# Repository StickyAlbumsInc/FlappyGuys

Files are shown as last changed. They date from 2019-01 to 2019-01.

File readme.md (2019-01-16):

Flappy Guys
==============

This repo contains the source code, materials list, STL files, patterns, and instructions for creating and assembling a group of 5 IR controlled, miniature "flappy guys," more boringly referred to as "air dancers" or "windsock people."

These guys, but small:



The inspiration for this project came about during a team meeting in which we lamented how loud and ineffective (and not remote controlled) current miniature "flappy guys" on the market are. We knew we could do it better! So this became a thing. Here is that thing.

The parts can add up, but many of them are things you'll probably have on hand already, if you work with Arduino. Many of the links on the parts are for bulk buying options, which gives you a little more up-front cost but a much lower cost-per-unit. If you plan to make a hobby out of Arduino, it's worth the investment, as these are common parts you will likely use often (header pins, DC jacks, solderable breadboards, etc.). 

It also helps if you have access to a 3D printer to print a shroud for each fan in your final build. If you can't 3D print one, you will need to fabricate a similar shroud in some fashion. There are a number of ways this could be done and some of those will be discussed in the build guide.

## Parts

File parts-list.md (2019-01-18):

Parts List
====

Essential Parts
----

These are the essential parts necessary for building the Flappy Guys array. 

* Arduino Uno - [link](https://www.amazon.com/Elegoo-EL-CB-001-ATmega328P-ATMEGA16U2-Arduino/dp/B01EWOE0UU)
* 12v DC power supply - [link](https://www.amazon.com/gp/product/B0725QLQH5)
* 5 90mm three-wire PWM PC cooling fans - [link](https://www.ebay.com/itm/90mm-3-pin-sleeve-Bearing-Computer-Case-cooling-Fan-plug-to-the-motherboard/302927138516)
* IR remote control and sensor board - [link](https://www.amazon.com/gp/product/B01EE4VXS0)
* 5 IRF530N MOSFET transisters - [link](https://www.ebay.com/itm/5Pcs-IRF530NPBF-IRF530N-TO-220-Ir-Power-Mosfet-US-Stock-v/132669538850)
* 18GA solid core wire
* 30x60in piece of ripstop nylon in a color of your choice (or multiple colors) - [link](https://www.amazon.com/gp/product/B07688SRPS)
* 24x36in sheet of black foam core - or some other material to construct the base (wood, plastic, metal) - buy this locally
* A few male-female Dupont jumper wires

Optional Parts
----

The parts below are optional, but having them will make your build easier and much cleaner. Without these parts, you could connect all of the pieces above with wire and solder them all together. Using the parts below, you'll be able to construct a board that all of your fans and your Arduino will plug into.

The build guide will assume you have the optional parts. If not, it's pretty easy to figure out how to omit them. 

* 5.5mm DC power jack - [link](https://www.amazon.com/gp/product/B01N5TW8P5/ref=ppx_yo_dt_b_asin_title_o03__o00_s01?ie=UTF8&psc=1)
* Solderable breadboard - [link](https://www.amazon.com/Gikfun-Solder-able-Breadboard-Plated-Arduino/dp/B071R3BFNL)
* Heat shrink tubing - [link](https://www.amazon.com/gp/product/B01M6YB9CB)
* Header pins - [link](https://www.amazon.com/Header-Lystaii-Pin-Connector-Electronic/dp/B06ZZN8L9S)
* 5 3-pin 10in CPU fan extension cables - [link](https://www.ebay.com/itm/10Pcs-12V-3-Pin-Female-to-3Pin-Male-PC-Fan-Power-Splitter-Extension-Cable-Wire/162980280013)

Tools & Misc. Materials
---
* 3D printer - [a great, affordable option](https://www.amazon.com/Anycubic-Upgraded-PRINTER-Heated-Screen/dp/B074NZPHJ5)
* Soldering iron - [my personal favorite](https://www.amazon.com/Bundle-Soldering-Station-CHP170-cutter/dp/B00AWUFVY8)
* Solder - [I use this](https://www.amazon.com/gp/product/B0006O933K)
* Breadboard - If you're confused on the wireing you can test before soldering
* Utility Knife (or Sword of Exact Zero)
* Carpenter's square or T-square (or a ruler and more patience)
* Compass (or 3in round lid, etc. to trace around) 

If your base is made of Foam Core:

* Hot glue gun & glue sticks
* E6000 Epoxy
* Straignt pins
* White glue
* Small paint brush
* Scissors
* Cutting Mat

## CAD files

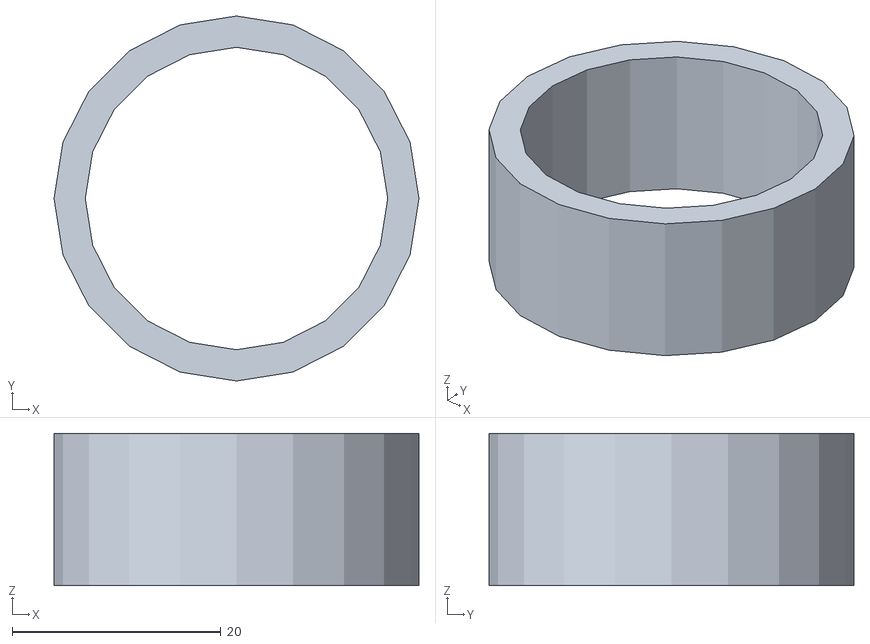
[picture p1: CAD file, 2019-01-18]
tension-ring.stl
35.0 x 35.0 x 14.6

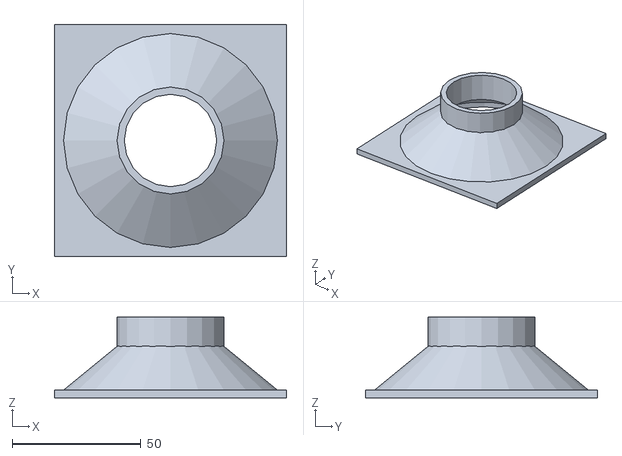
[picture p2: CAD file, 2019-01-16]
fan-shroud.stl
90.0 x 90.0 x 31.3

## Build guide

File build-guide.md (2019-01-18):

Build Guide
=============

1. Setting Up The IR Sensor
2. Updating Up The Control Code
3. Prototyping Single Fan Writing
4. Building The Control Board
5. Connecting & Testing
6. Fabricating The Fan Shrouds
7. Constructing Nylon Flappy Guys
8. Building The Base
9. Putting It All Together

### 1. Setting Up The IR Sensor

Let's go ahead and get the code side of this project out of the way, since it's the easiest. The pvodied `control-code.ino` file contains everything you need to start/stop your five flappy guys, but you'll probably need to change the IR input values, depending on your IR remote. 

So the first step is finding these values.

To do this, first begin by plugging your IR receiver into your Arduino. This shouldn't be a parmanent connection at this point, just temporarily connect the IR receiver with jumper wires as indicated below.

IR Wiring

Next, plug your Arduino into your computer and open `ir-read-utility.ino` in your Arduino IDE. In the tools menu, make sure you have the right COM port selected and flash the read utility code to your Arduino. 

Once you've flashed the board, open the serial monitor (Tools > Serial Monitor). 

Now start pressing buttons on your remote. In my build, I used buttons 1-5 to control each of the 5 fans, and used a big red center button in the middle of the remote to toggle everything off/on. 

It doesn't really matter what order you assign buttons in, so long as it's logical to you. Using numbers 1-5 makes the most sense, though, so I'll assume you're doing that! 

Whenever you press a button on the remote, you should see an integer displayed in the serial monitor. You'll want to make note of which integers belong to which buttons.

Please note, with these inexpensive IR sensors, it's very easy to get interference. As I was working on this, my heartrate sensor from my Fitbit kept interfering with the IR sensor when my wrist was next to it. 

So push buttons a few times and make sure you're getting consistent readings! Recode those numbers and ignore any inconsistencies, as they indicate interference with the IR signal. 

### 2. Updating The Control Code

Once you've made note of all of your buttons and their corresponding integers, you can open `control-code.stl` and update the values listed there to match the output from your remote. 

On lines 48 and 49, you'll find two variables:

`fanBtns` - This is an array of 5 buttons to toggle fans. Put your 1-5 IR codes in there, in order.
`allFansBtn` - This is the button that will turn all fans on/off at once. Put your toggle button IR code in there.

Once you've updated these variables and safed the file, you can flash `control-code.ino` to your Arduino, overwriting the previous IR read utility code. 

One other important thing to make note of here is the output pins used to control the fan. In the control code, pins are configured as follows:

* Pin 3 -> Fan 1
* Pin 5 -> Fan 2
* Pin 6 -> Fan 3
* Pin 9 -> Fan 4
* Pin 10 -> Fan 5
* Pin 11 -> IR Receiver

You can change these if you wish, but for the purposes of this guide, I'll assume you haven't.

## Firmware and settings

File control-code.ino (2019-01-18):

// Download the IRremote library from here:
// https://github.com/z3t0/Arduino-IRremote
// and put it in your Arduino libraries folder.
#include <IRremote.h>

// FanGates control MOSFET transistors associated with
// thee pins.
int fanGates[5] = {3,5,6,9,10};

// Individual states for each Gate (on 1/off 0)
int fanState[5]  = {0}; 

// Array of power levels for each fan
int fanSpeeds[5] = {0};

// Adjust power levels as-needed based on fan speed
// and strength. You may find you need a much lower
// "low" speed and a much higher "high" speed. Values
// range from 1-255.

// Power level for fan on high speed
int highPower = 180;

// Power level for fan on low speed
int lowPower = 50;

// Millisecond delay storage vars for the IR receiver
// and fan speed control timing
unsigned long prevIrMs = 0; 
unsigned long prevFanMs[5] = {0}; 

// Duration intervals for IR read and fan motor speeds
int irInterval = 1000;
int fanInterval = 2000; 

// Receive input from IR remote on this pin
int irPin = 11;

// Each fan is controlled invidually by its own button on the remote
// control. There's also one button that turns off all of the fans.
//  You'll need to update these values to match the raw data
// coming from your particular remote control. 
//
// See the build guide and ir-read-utility.ino for instructions on how
// to obtain these values.

// Raw ints from the IR remote
int fanBtns[5] = {16753245,16736925,16769565,16720605,16712445};
int allFansBtn = 14535; // This button turns off all fans

// Set up the receiver
IRrecv irrecv(irPin);
decode_results results;

void setup() {
  // Start the IR receiver 
  irrecv.enableIRIn();

  // Set pin modes and initial state for Fan gates
  for (int i = 0; i < 5; i = i + 1) {
    pinMode(fanGates[i], OUTPUT);
    digitalWrite(fanGates[i], LOW);
  }
}

void loop() {
  // Run control loop on each fan
  for (int i = 0; i < 5; i = i + 1) {
    control_fan(i);
  }

  // Toggle fan state if we receive IR input
  if (irrecv.decode(&results)) {
    toggle_fan_state(results.value);
    unsigned long currentMs = millis();

    // Delay reading more IR input for the duration of
    // the IR interval - basically debouce IR
    if (currentMs - prevIrMs >= irInterval) {
      // Update millisecond storage var and restart
      // reading of IR input
      prevIrMs = currentMs;
      irrecv.resume();
    }
  }
}

// Set fan states based on IR input.
void toggle_fan_state(int fan) {
  // Toggle all fans "off" if one or more is running, or all "on" if
  // no fans are running.
  if (fan == allFansBtn) {
    int current_state = 0;
    for (int i = 0; i < 5; i = i + 1) {
      current_state = current_state + control_fan(i);
    }

    if (current_state > 0) {
      for (int i = 0; i < 5; i = i + 1) {
        fanState[i] = 0;
      }
    } else {
      for (int i = 0; i < 5; i = i + 1) {
        fanState[i] = 1;
      }
    }
  // Control fans individually
  } else {  
    // Find the fan gate that corresponds to the button.
    int index = 100; // Default out of range value
    for (int i = 0; i < 5; i = i + 1) {
      if (fanBtns[i] == fan) {
        index = i;
      }
    }
      
    // Ignore any uncomfigured buttons (index still out
    // of range)
    if (index < 100) {
      fanState[index] = (fanState[index] == 0)? 1 : 0;  
    }
  }
}

// Control fan gates based on timing and their state as
// set via remote input.
void control_fan(int fan) {
  // If the fan gate has been toggled on, get current
  // millisecond timestamp and set fan motor to either
  // high speed or low speed depending on timing.
  if(fanState[fan] == 1) {
    unsigned long currentMs = millis();
    if (currentMs - prevFanMs[fan] >= fanInterval) {
      prevFanMs[fan] = currentMs;
      if(fanSpeeds[fan] != highPower) {
        fanSpeeds[fan] = highPower;
        analogWrite(fanGates[fan], highPower);
        fanInterval = random(2000,4000);
      } else {
        fanSpeeds[fan] = lowPower;
        analogWrite(fanGates[fan], lowPower);
        fanInterval = random(1000,2000);
      }
    }
  // If the fan gate has been toggled off, set its
  // pin to LOW, toggling the gate.
  } else {
    if(fanSpeeds[fan] > 0) {
      fanSpeeds[fan] = 0;
      digitalWrite(fanGates[fan], LOW);
    }
  }
}

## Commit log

2019-01-16 initial input
    [fan-shroud.stl]
2019-01-18 adding tension ring stl file
    [tension-ring.stl]
2019-01-18 update tension ring with new dimensions that account for PLA plastic shrinkage
    [tension-ring.stl]
2019-01-18 explain fan pinout
